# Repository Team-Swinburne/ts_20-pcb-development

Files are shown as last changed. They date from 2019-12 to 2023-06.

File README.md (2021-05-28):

# TS_20 PCB Development

This is the official repository for the PCB development of Team Swinburne FSAE 2020

## Installation & Usage

## Contributing
Pull requests are welcome. For major changes, please open an issue first to discuss what you would like to change.

Please make sure to update tests as appropriate.

## License
[MIT](https://choosealicense.com/licenses/mit/)

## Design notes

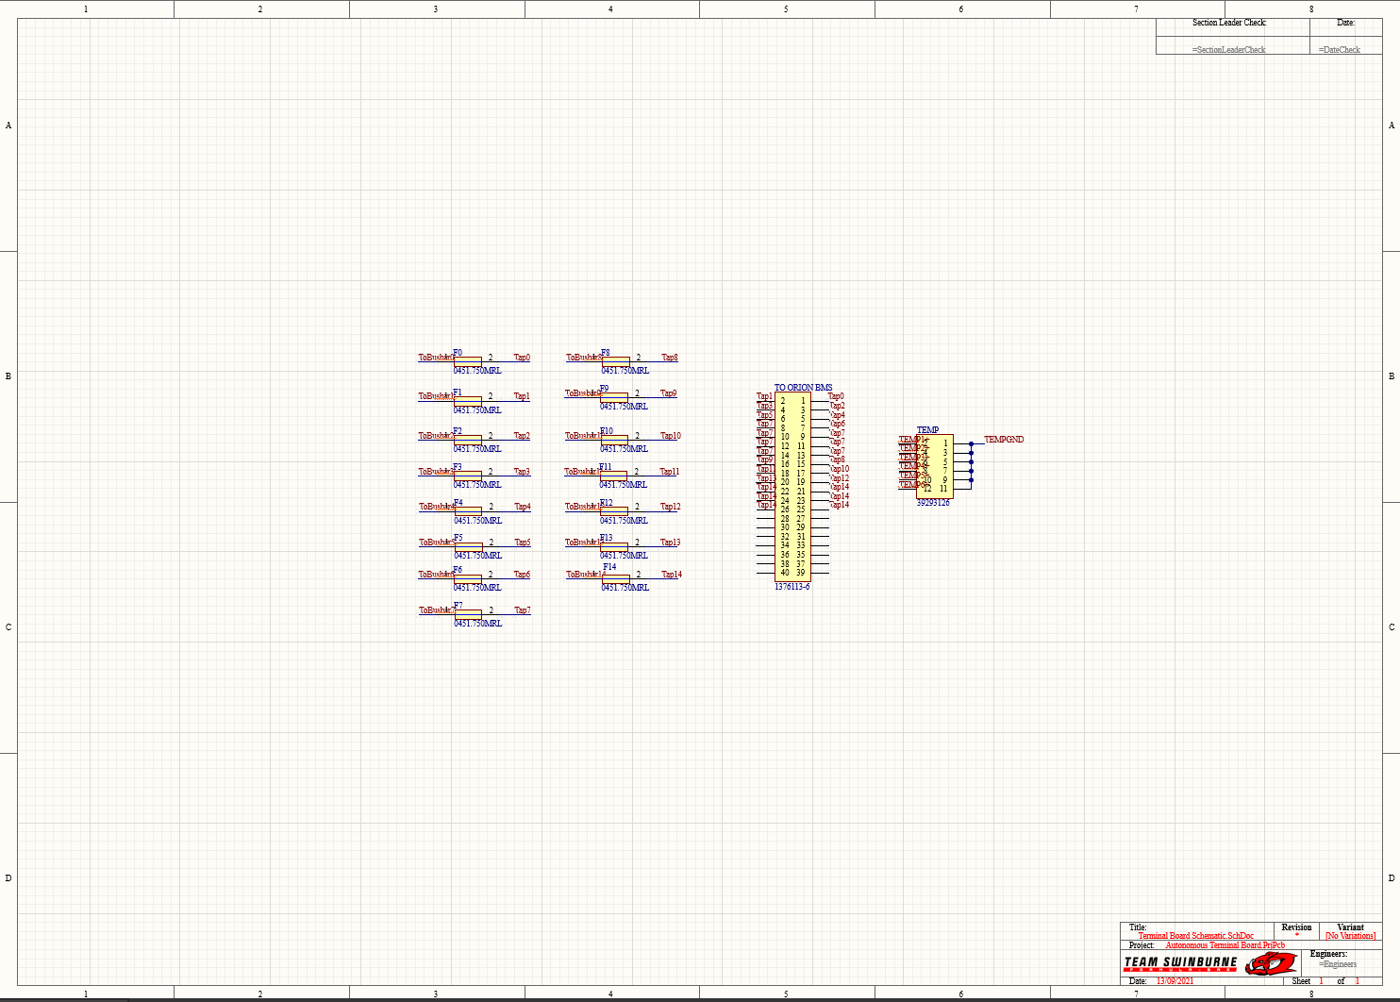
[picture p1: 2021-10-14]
ts_20_Autonomous-Terminal-Board/Autonomous Terminal Board/Photos/Schematic 13 Sep.PNG

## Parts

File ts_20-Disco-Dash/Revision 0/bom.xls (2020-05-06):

Comment | Description | Designator | Footprint | LibRef | Quantity | Colour | Digikey Part Number | Value
LED | Red LED Indication - Discrete 1.75V 0805 (2012 Metric) | 5V ACTIVE, 5V ACTIVE (ISO) | 0805 LED | SML-210LTT86 | 2 | Red | 511-1286-1-ND
RED | LED RED CLEAR 5MM ROUND T/H | AMS, BSPD, IMD, PDOC | 5MM LED | C503B-GAN-CB0F0791 | 4 | Green | C503B-GAN-CB0F0791-ND
10nF |  | C8_U_CAN1, C8_U_CAN2, C11_U_CAN1, C11_U_CAN2 | 1206 | GCM3195C2A103JA16D | 4 |  | 490-4978-2-ND | 10nF
100nF |  | C9_U_CAN1, C9_U_CAN2, C10_U_CAN1, C10_U_CAN2, C13_U_CAN1, C13_U_CAN2, C15_U_CAN1, C15_U_CAN2 | 805 | GCM21BR71E104KA37L | 8 |  |  | 100nF
10uF |  | C12_U_CAN1, C12_U_CAN2, C14_U_CAN1, C14_U_CAN2, C20 | 805 | GRM21BR6YA106KE43L | 5 |  | 490-10514-6-ND | 10uF
100pF |  | C16_U_CAN1, C16_U_CAN2, C17_U_CAN1, C17_U_CAN2, C18_U_CAN1, C18_U_CAN2, C19_U_CAN1, C19_U_CAN2 | 805 | GCM21B5C1H101JA37L | 8 |  |  | 100pF
22uF |  | C21 | 805 | GRM21BR61A226ME51L | 1 |  | 490-10511-1-ND | 22uF
Red | Red LED Indication - Discrete 1.75V 0805 (2012 Metric) | D1, D3, D4, D5, D6, D8, D9, D10, D11, D12, D13, D14 | 0805 LED | SML-210LTT86 | 12 | Red | 511-1286-1-ND
SD560BTR | 1.2V_F 600V 5A SMB | D2 | SMB Diode | SD560BTR | 1 |  | 1655-1530-2-ND
SMAZ5V6-13-F | DIODE ZENER 5.6V 1W SMA | D7 | DI SMA Diode | SMAZ5V6-13-F | 1 |  | SMAZ5V6-FDICT-ND
0ZCF0200AF2C | SMD 24V 2A Fuse | F1 | 2920 | 0ZCF0200AF2C | 1 |  | 507-1749-2-ND
39281063 | Mini-Fit VERT 3x2 | P? | 39281063 | 39281063 | 1 |  | WM3802-ND
BC817-16LT1 | 300mW BJT NPN Transistor | Q1, Q2, Q3, Q4 | ON SOT-23 BJT | BC817-16LT1 | 4 |  | BC817-16LT1OSTR-ND
240R |  | R1, R2, R3, R4 | 805 | RC0805FR07240RL | 4 |  |  | 240R
680R |  | R8, R9, R10, R15 | 805 | RC0805FR07680RL | 4 |  |  | 680R
1k |  | R11, R12, R13, R14 | 805 | RC0805FR071KL | 4 |  |  | 1k
0R |  | R23_U_CAN1, R23_U_CAN2 | 805 | RC0805FR070RL | 2 |  |  | 0R
1.5k |  | R34, R35 | 805 | RC0805FR071K5L | 2 |  |  | 1.5k
DISCO-F469NI | STM32F469 Discovery STM32F4 ARM® Cortex®-M4 MCU 32-Bit Embedded Evaluation Board (The Disco 69 lol) | U1 | DISCO-F469NI | DISCO-F469NI | 1 |  | 497-15990-ND
ADM3053 | Isolated CAN Transceiver | U2_U_CAN1, U2_U_CAN2 | AD SOIC-W 20 | ADM3053 | 2 |  | ADM3053BRWZ-ND
B82787C0104H002 | Common mode choke intended for CANBUS 150mA 50V) | U3_U_CAN1, U3_U_CAN2 | TDK 4-PC Pad | B82787C0104H002 | 2 |  | 495-4598-2-ND
NUP2105L | Dual Line CAN Bus Protector | U4_U_CAN1, U4_U_CAN2 | ON SOT-23 | NUP2105L | 2 |  | NUP2105LT1GOSCT-ND
R-78C5.0-1.0 | CONV DC/DC 1A 5V OUT SIP VERT | U9 | RECOM 3-SIP | R-78C5.0-1.0 | 1 |  | 945-1395-5-ND
RI-0505S | 5V DC-DC Converter (2W) | U10 | RECOM 4-SIP | RI-0505S | 1 |  | 945-1189-ND
744272121 | Common Mode Choke 120UH 2.5A 2LN 460 OHM SMD | U11 | Wurth 4-PC Pad | 744272121 | 1 |  | 732-1489-2-ND
DT13-12P |  | UNIVERSAL1 | DT13-12P | DT13-12P[[/\]]DT13-12P | 1 |  | 1734-1451-ND

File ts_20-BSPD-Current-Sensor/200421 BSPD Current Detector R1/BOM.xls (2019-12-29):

Comment | Description | Designator | Footprint | LibRef | Quantity | Colour
0mm |  | 0V, 5kW OUT, 5V, GLV+, POST AMP, PREAMP, REF | TH Test Point | TH Test Point | 7
10uF |  | C1 | 805 | GRM21BR6YA106KE43L | 1
22uF |  | C2 | 1206 | CC1206MKX5R7BB226 | 1
100nF |  | C3, C4, C5, C6 | 805 | GCM21BR71E104KA37L | 4
SD560BTR | 1.2V_F 600V 5A SMB | D1 | SMB Diode | SD560BTR | 1
Blue | LED BLUE CLEAR 2012 SMD | D2 | 0805 LED | SML-MN2BCTT86C | 1 | Blue
0ZCF0200AF2C | SMD 24V 2A Fuse | F1 | 2920 | 0ZCF0200AF2C | 1
26013115 |  | P1 | 26013115 | 26013115 | 1
DT13-12P |  | P4 | DT13-12P | DT13-12P[[/\]]DT13-12P | 1
30k |  | PULL DOWN! | 805 | RC0805FR0730KL | 1
2N7002K | 60V 380mA, NFET MOSTFET (Small Signal) | Q1 | ON SOT-23 MOSFET | 2N7002K | 1
10k |  | R1 | 805 | RC0805FR0710KL | 1
1k |  | R2, R5 | 805 | RC0805FR071KL | 2
10K (Var) |  | R3 | B 3296 | 3296W-1-103LF | 1
100R |  | R4 | 805 | RC0805FR07100RL | 1
1.5k |  | R6 | 805 | RC0805FR071K5L | 1
3k |  | R7 | 805 | RC0805FR073KL | 1
R-78C5.0-1.0 | CONV DC/DC 1A 5V OUT SIP VERT | U1 | RECOM 3-SIP | R-78C5.0-1.0 | 1
744272121 | Common Mode Choke 120UH 2.5A 2LN 460 OHM SMD | U2 | Wurth 4-PC Pad | 744272121 | 1
LMV339IDR | Comparator General Purpose Open Collector 14-SOIC | U3 | TI 14-SOIC | LMV339IDR | 1
LM324D | IC OPAMP GP 4 CIRCUIT 14SOIC | U4 | TI 14-SOIC | LM324D | 1

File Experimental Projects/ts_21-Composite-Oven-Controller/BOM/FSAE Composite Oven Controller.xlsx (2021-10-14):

Comment | Description | Designator | Footprint | Quantity | Supplier 1 | Supplier Part Number 1
0mm |  | 3.3V, 5V, GND, OD1, OI1, OS, Oven inc 1, Oven set | SMD Test Point | 11
Boot jumper |  | BOOT | TH 2.54mm Header 2x3 | 1
10uF |  | C1 | 0805 | 1
100nF |  | C2, C4, C10, C11, C12, C13 | 0805 | 6
1uF |  | C3, C5, C9 | 0805 | 3
22nF |  | C6 | 0805 | 1
22pF |  | C7, C8 | 0805 | 2
SD560BTR | 1.2V_F 600V 5A SMB | D1 | SMB Diode | 1 |  | 1655-1530-2-ND
Red | Red LED Indication - Discrete 1.75V 0805 (2012 Metric) | D2, D3 | 0805 LED | 2 |  | 511-1286-1-ND, [NoParam]
ST7735 header | Header for the ST7735 LCD module | LCD | TH 2.54mm Header 1x8 | 1 | Digi-Key | 1528-1536-ND
DT13-4P |  | P1 | DT13-4P | 1
10M |  | R1 | 0805 | 1
1k |  | R2, R3, R6, R8, R11 | 0805 | 5
5.1k |  | R4, R5, R9, R10 | 0805 | 4
10k |  | R7, R12, R13, R14, R15 | 0805 | 5
Rotary Encoder |  | S1 | Rotary Encoder | 1 | Digi-Key | PEC11R-4220K-S0024-ND
STLINK 2.54mm | Header used for the STLINK programmer | STLINK | TH 2.54mm Header 1x4 | 1
STM32F103C8T6 | ARM® Cortex®-M3 STM32F1 Microcontroller IC 32-Bit 72MHz 64KB (64K x 8) FLASH | U1 | STM 48-LQFP | 1 | Digi-Key | 497-6063-ND
RT9193-33GB |  | U2 | SOT23-5 IPC | 1 | Digi-Key | 1028-1014-1-ND
TLP291(Y-TP,SE |  | U3, U4, U5 | SOIC-4 (4.55mm width) | 3 | Digi-Key | TLP291(Y-TPSECT-ND
24FC01T-E/OT | I2C EEPROM | U6 | SOT23-5 IPC | 1 | Digi-Key | 24FC01T-E/OTCT-ND
UART 2.54mm |  | UART | TH 2.54mm Header 1x3 | 1
USB4085-GF-A |  | USB | USB4085-GF-A | 1
8MHz |  | X1 | Abracon HC-49/US | 1 | Digi-Key | 535-10212-2-ND

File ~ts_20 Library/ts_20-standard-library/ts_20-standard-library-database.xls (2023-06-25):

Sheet: Fuses
Manufacturer | Part Number | Description | Library Ref | Library Path | Footprint Ref | Footprint Path | Digikey Part Number | Digikey Link
LittelFuse Inc | RKEF300 | 60V 3A Reset Fuse | PTC Fuse | analogue.SchLib | 5mm Leaded | through.PcbLib | RKEF300HF-ND | https://www.digikey.com/product-detail/en/littelfuse-inc/RKEF300/RKEF300HF-ND/5130274
Bel Fuse Inc | 0ZCF0200AF2C | SMD 24V 2A Fuse | PTC Fuse | analogue.SchLib | 2920 | surface.PcbLib | 507-1749-2-ND | https://www.digikey.com/product-detail/en/bel-fuse-inc/0ZCF0200AF2C/507-1749-2-ND/4156090
LittelFuse Inc | 0154.750DR | FUSE BOARD MNT 750MA 125VAC/VDC | Fuse | analogue.SchLib | Omni BLOK 0154 | surface.PcbLib | F1221CT-ND | https://www.digikey.com/product-detail/en/littelfuse-inc/0154.750DR/F1221CT-ND/183370
Littelfuse Inc. | 01530008Z | FUSE HOLDER BLADE 32V 15A PCB | PTC Fuse | analogue.SchLib | LF Holder | through.PcbLib | F065-ND | https://www.digikey.com.au/product-detail/en/littelfuse-inc/01530008Z/F065-ND/183334
Littelfuse Inc. | 0ZCF0100AF2A | PTC RESET FUSE 60V 1A 292 | PTC Fuse | analogue.SchLib | 2920 | surface.PcbLib | 507-2070-1-ND | https://www.digikey.com/product-detail/en/bel-fuse-inc/0ZCF0100AF2A/507-2070-1-ND/6210547

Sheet: Inductors
Manufacturer | Part Number | Description | Value | Impedence | Tolerance | Material | Rated Current | Library Ref | Library Path | Footprint Ref | Footprint Path | Digikey Part Number | Digikey Link
TDK Corportation | MMZ2012Y202BTD25 |  | Ferrite | 2 kOhms @ 100MHz |  | Ferrite Bead | 400mA | Inductor | analogue.SchLib | 0805 | surface.PcbLib | 445-172872-1-ND
Recom | RLS-126 |  | 12uH | 230mOhm | 20% | Wirewound | 800mA | Inductor | analogue.SchLib | 1812 | surface.PcbLib | 945-3429-ND
EPCOS (TDK) | B82787C0104H002 | 100µH @ 100kHz 2 Line Common Mode Choke Surface Mount 5.8 kOhms @ 10MHz 150mA DCR 2Ohm | 100µH @ 100kHz | 5.8 kOhms @ 10MHz |  | Wirewound | 150mA | B82787C0104H002 | integrated.SchLib | TDK 4-PC Pad | surface.PcbLib | 495-4598-1-ND | https://www.digikey.com/product-detail/en/epcos-tdk/B82787C0104H002/495-4598-2-ND/3680998
Wurth Electronics Inc | 744272121 | 120µH @ 100kHz 2 Line Common Mode Choke Surface Mount 460 Ohms @ 30MHz 2.5A DCR 25mOhm | 120uH @ 100kHz | 460 Ohms @ 30MHz |  | Wirewound | 2.5A | 744272121 | integrated.SchLib | Wurth 4-PC Pad | surface.PcbLib | 732-1489-1-ND | https://www.digikey.com/product-detail/en/w-rth-elektronik/744272121/732-1489-1-ND/1639501
Wurth Electronics Inc | 744273501 | 5µH @ 100kHz 2 Line Common Mode Choke Surface Mount 500 Ohms @ 130MHz 5A DCR 5.5mOhm | 5µH @ 100kHz | 500 Ohms @ 130MHz |  | Wirewound | 5A | 744273501 | integrated.SchLib | Wurth 4-PC Pad | surface.PcbLib | 732-2214-6-ND | https://www.digikey.com/product-detail/en/w-rth-elektronik/744273501/732-2214-6-ND/2175826

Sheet: Resistors
Manufacturer | Part Number | Value | Tolerance | Material | Rated Voltage | Library Ref | Library Path | Footprint Ref | Footprint Path | Digikey Part Number
YAGEO | RC0805FR070RL | 0R | 1% | FR-07 | 0.125W | Resistor | analogue.SchLib | 0805 | surface.PcbLib | 311-0.0CRCT-ND
YAGEO | RC0805FR071RL | 1R | 1% | FR-07 | 0.125W | Resistor | analogue.SchLib | 0805 | surface.PcbLib | 311-1.00CRCT-ND
YAGEO | RC0805FR071R2L | 1.2R | 1% | FR-07 | 0.125W | Resistor | analogue.SchLib | 0805 | surface.PcbLib | 311-1.20CRCT-ND
YAGEO | RC0805FR071R3L | 1.3R | 1% | FR-07 | 0.125W | Resistor | analogue.SchLib | 0805 | surface.PcbLib | 311-1.30CRCT-ND
YAGEO | RC0805FR071R5L | 1.5R | 1% | FR-07 | 0.125W | Resistor | analogue.SchLib | 0805 | surface.PcbLib | 311-1.50CRCT-ND
YAGEO | RC0805FR071R6L | 1.6R | 1% | FR-07 | 0.125W | Resistor | analogue.SchLib | 0805 | surface.PcbLib | 311-1.60CRCT-ND
YAGEO | RC0805FR071R8L | 1.8R | 1% | FR-07 | 0.125W | Resistor | analogue.SchLib | 0805 | surface.PcbLib | 311-1.80CRCT-ND
YAGEO | RC0805FR072RL | 2R | 1% | FR-07 | 0.125W | Resistor | analogue.SchLib | 0805 | surface.PcbLib | 311-2.00CRCT-ND
YAGEO | RC0805FR072R2L | 2.2R | 1% | FR-07 | 0.125W | Resistor | analogue.SchLib | 0805 | surface.PcbLib | 311-2.20CRCT-ND
YAGEO | RC0805FR072R4L | 2.4R | 1% | FR-07 | 0.125W | Resistor | analogue.SchLib | 0805 | surface.PcbLib | 311-2.40CRCT-ND
YAGEO | RC0805FR072R7L | 2.7R | 1% | FR-07 | 0.125W | Resistor | analogue.SchLib | 0805 | surface.PcbLib | 311-2.70CRCT-ND
YAGEO | RC0805FR073RL | 3R | 1% | FR-07 | 0.125W | Resistor | analogue.SchLib | 0805 | surface.PcbLib | 311-3.00CRCT-ND
YAGEO | RC0805FR073R3L | 3.3R | 1% | FR-07 | 0.125W | Resistor | analogue.SchLib | 0805 | surface.PcbLib | 311-3.30CRCT-ND
YAGEO | RC0805FR073R6L | 3.6R | 1% | FR-07 | 0.125W | Resistor | analogue.SchLib | 0805 | surface.PcbLib | 311-3.60CRCT-ND
YAGEO | RC0805FR073R9L | 3.9R | 1% | FR-07 | 0.125W | Resistor | analogue.SchLib | 0805 | surface.PcbLib | 311-3.90CRCT-ND
YAGEO | RC0805FR074R3L | 4.3R | 1% | FR-07 | 0.125W | Resistor | analogue.SchLib | 0805 | surface.PcbLib | 311-4.30CRCT-ND
YAGEO | RC0805FR074R7L | 4.7R | 1% | FR-07 | 0.125W | Resistor | analogue.SchLib | 0805 | surface.PcbLib | 311-4.70CRCT-ND
YAGEO | RC0805FR075R1L | 5.1R | 1% | FR-07 | 0.125W | Resistor | analogue.SchLib | 0805 | surface.PcbLib | 311-5.10CRCT-ND
YAGEO | RC0805FR075R6L | 5.6R | 1% | FR-07 | 0.125W | Resistor | analogue.SchLib | 0805 | surface.PcbLib | 311-5.60CRCT-ND
YAGEO | RC0805FR076R2L | 6.2R | 1% | FR-07 | 0.125W | Resistor | analogue.SchLib | 0805 | surface.PcbLib | 311-6.20CRCT-ND
YAGEO | RC0805FR076R8L | 6.8R | 1% | FR-07 | 0.125W | Resistor | analogue.SchLib | 0805 | surface.PcbLib | 311-6.80CRCT-ND
YAGEO | RC0805FR077R5L | 7.5R | 1% | FR-07 | 0.125W | Resistor | analogue.SchLib | 0805 | surface.PcbLib | 311-7.50CRCT-ND
YAGEO | RC0805FR078R2L | 8.2R | 1% | FR-07 | 0.125W | Resistor | analogue.SchLib | 0805 | surface.PcbLib | 311-8.20CRCT-ND
YAGEO | RC0805FR079R1 | 9.1R | 1% | FR-07 | 0.125W | Resistor | analogue.SchLib | 0805 | surface.PcbLib | 311-9.10CRCT-ND
YAGEO | RC0805FR0710RL | 10R | 1% | FR-07 | 0.125W | Resistor | analogue.SchLib | 0805 | surface.PcbLib | 311-10.0CRCT-ND
YAGEO | RC0805FR0711RL | 11R | 1% | FR-07 | 0.125W | Resistor | analogue.SchLib | 0805 | surface.PcbLib | 311-11.0CRCT-ND
YAGEO | RC0805FR0712RL | 12R | 1% | FR-07 | 0.125W | Resistor | analogue.SchLib | 0805 | surface.PcbLib | 311-12.0CRCT-ND
YAGEO | RC0805FR0713RL | 13R | 1% | FR-07 | 0.125W | Resistor | analogue.SchLib | 0805 | surface.PcbLib | 311-13.0CRCT-ND
YAGEO | RC0805FR0715RL | 15R | 1% | FR-07 | 0.125W | Resistor | analogue.SchLib | 0805 | surface.PcbLib | 311-15.0CRCT-ND
YAGEO | RC0805FR0716RL | 16R | 1% | FR-07 | 0.125W | Resistor | analogue.SchLib | 0805 | surface.PcbLib | 311-16.0CRCT-ND
YAGEO | RC0805FR0718RL | 18R | 1% | FR-07 | 0.125W | Resistor | analogue.SchLib | 0805 | surface.PcbLib | 311-18.0CRCT-ND
YAGEO | RC0805FR0720RL | 20R | 1% | FR-07 | 0.125W | Resistor | analogue.SchLib | 0805 | surface.PcbLib | 311-20.0CRCT-ND
YAGEO | RC0805FR0722RL | 22R | 1% | FR-07 | 0.125W | Resistor | analogue.SchLib | 0805 | surface.PcbLib | 311-22.0CRCT-ND
YAGEO | RC0805FR0724RL | 24R | 1% | FR-07 | 0.125W | Resistor | analogue.SchLib | 0805 | surface.PcbLib | 311-24.0CRCT-ND
YAGEO | RC0805FR0727RL | 27R | 1% | FR-07 | 0.125W | Resistor | analogue.SchLib | 0805 | surface.PcbLib | 311-27.0CRCT-ND

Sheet: Diodes
Manufacturer | Description | Vf | Vbr | Part Number | Library Ref | Library Path | Footprint Ref | Footprint Path | Digikey Part Number | Digikey Link | Alternative Parts
SMC Diode Solutions | 1.2V_F 600V 5A SMB |  |  | SD560BTR | Diode | analogue.SchLib | SMB Diode | surface.PcbLib | 1655-1530-2-ND | https://www.digikey.com/product-detail/en/smc-diode-solutions/SD560BTR/1655-1530-2-ND/6022620
Diodes Inc | 18V Zener 1W SND |  |  | SMAZ18-13-F | Zener Diode | analogue.SchLib | SMA Diode | surface.PcbLib | SMAZ18-FDITR-ND | https://www.digikey.com/product-detail/en/diodes-incorporated/SMAZ18-13-F/SMAZ18-FDITR-ND/814767
On Semiconductor | Zener Diode 5.1V 500mW ±5% Surface Mount SOD-123 |  |  | MMSZ5231B-TP | Zener Diode | analogue.SchLib | SOD-123 Diode | surface.PcbLib | MMSZ5231B-TPMSCT-ND | https://www.digikey.com/product-detail/en/micro-commercial-co/MMSZ5231B-TP/MMSZ5231B-TPMSCT-ND/1793361
Diodes Inc | DIODE ZENER 12.43V 500MW SOD323F |  |  | DDZ13ASF-7 | Zener Diode | analogue.SchLib | DI SOD-323F Diode | surface.PcbLib | DDZ13ASF-7DICT-ND | https://www.digikey.com/product-detail/en/diodes-incorporated/DDZ13ASF-7/DDZ13ASF-7DICT-ND/3451540
Diodes Inc | DIODE ZENER 5.6V 1W SMA |  |  | SMAZ5V6-13-F | Zener Diode | analogue.SchLib | DI SMA Diode | surface.PcbLib | SMAZ5V6-FDICT-ND | https://www.digikey.com/product-detail/en/diodes-incorporated/SMAZ5V6-13-F/SMAZ5V6-FDICT-ND/755500
Diodes Inc | DIODE ZENER 51V 3W SMB |  |  | 1SMB5942B-13 | Zener Diode | analogue.SchLib | DI SMB Diode | surface.PcbLib | 1SMB5942B-13DICT-ND | https://www.digikey.com/product-detail/en/diodes-incorporated/1SMB5942B-13/1SMB5942B-13DICT-ND/5054245
On Semiconductor | DIODE GEN PURP 100V 200MA SOD80 |  |  | FDLL4148-D87Z | Diode | analogue.SchLib | SOD-80 Diode | surface.PcbLib | FDLL4148-D87ZCT-ND | https://www.digikey.com/product-detail/en/on-semiconductor/FDLL4148-D87Z/FDLL4148-D87ZCT-ND/3042567
ST | 42.8V Clamp 93A (8/20µs) Ipp Tvs Diode Surface Mount SMB (DO-214AA) | 42.8 | 42.8V | SM6T39CAY | Bidirectional Zener Diode | analogue.SchLib | ST SMB Diode | surface.PcbLib | SM6T39CAY | https://www.digikey.com/en/products/detail/stmicroelectronics/SM6T39CAY/2442903 | https://www.digikey.com/en/products/detail/stmicroelectronics/SM6T39AY/2442901

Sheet: LEDs
Manufacturer | Part Number | Description | Colour | Library Ref | Library Path | Footprint Ref | Footprint Path | Digikey Part Number | Digikey Link
Cree Inc. | C503B-GAN-CB0F0791 | LED GREEN CLEAR 5MM ROUND T/H | Green | LED | analogue.SchLib | 5MM LED | through.PcbLib | C503B-GAN-CB0F0791-ND | https://www.digikey.com/products/en?mpart=C503B-GAN-CB0F0791&v=90
Broadcom Limited | HSMM-C150 | LED GREEN DIFFUSED CHIP SMD | Green | LED | analogue.SchLib | 1206 LED GREEN | surface.PcbLib | HSMM-C150-ND | https://www.digikey.com/product-detail/en/broadcom-limited/HSMM-C150/HSMM-C150-ND/1234707
Broadcom Limited | HSMC-C150 | LED RED DIFFUSED CHIP SMD | Red | LED | analogue.SchLib | 1206 LED RED | surface.PcbLib | 516-2825-6-ND | https://www.digikey.com/product-detail/en/broadcom-limited/HSMC-C150/516-2825-6-ND/3909256
ROHM Semiconductor | SML-210FTT86 | Green LED Indication - Discrete 1.75V 0805 (2012 Metric) | Green | LED | analogue.SchLib | 0805 LED | surface.PcbLib | 511-1285-1-ND | https://www.digikey.com/product-detail/en/rohm-semiconductor/SML-210FTT86/511-1285-1-ND/637098
ROHM Semiconductor | SML-211DTT86 | Orange LED Indication - Discrete 1.75V 0805 (2012 Metric) | Orange | LED | analogue.SchLib | 0805 LED | surface.PcbLib | 511-1291-1-ND | https://www.digikey.com/product-detail/en/rohm-semiconductor/SML-211DTT86/511-1291-1-ND/637104
ROHM Semiconductor | SML-211YTT86 | Yellow LED Indication - Discrete 1.75V 0805 (2012 Metric) | Yellow | LED | analogue.SchLib | 0805 LED | surface.PcbLib | 511-1293-1-ND | https://www.digikey.com/product-detail/en/rohm-semiconductor/SML-211YTT86/511-1293-1-ND/637106
ROHM Semiconductor | SML-210LTT86 | Red LED Indication - Discrete 1.75V 0805 (2012 Metric) | Red | LED | analogue.SchLib | 0805 LED | surface.PcbLib | 511-1286-1-ND | https://www.digikey.com/product-detail/en/rohm-semiconductor/SML-210LTT86/511-1286-1-ND/637099
ROHM Semiconductor | SML-MN2BCTT86C | LED BLUE CLEAR 2012 SMD | Blue | LED | analogue.SchLib | 0805 LED | surface.PcbLib | 846-1207-1-ND | https://www.digikey.com/product-detail/en/rohm-semiconductor/SMLMN2BCTT86C/846-1207-1-ND/6057239
 |  |  | RGB | LED | analogue.SchLib | HOTRED RGB_LED | surface.PcbLib |  | https://www.aliexpress.com/item/32943617217.html?spm=a2g0s.9042311.0.0.99a74c4d1Dy1p4

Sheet: Transistors
Manufacturer | Part Number | Description | Library Ref | Library Path | Footprint Ref | Footprint Path | Digikey Part Number | Digikey Link | Qty
ON Semiconductor | 2N7002K | 60V 380mA, NFET MOSTFET (Small Signal) | MOSFET-N | analogue.SchLib | ON SOT-23 MOSFET | surface.PcbLib | 2N7002KCT-ND | https://www.digikey.com/product-detail/en/on-semiconductor/2N7002K/2N7002KCT-ND/2060375 | 30
ON Semiconductor | BC817-16LT1 | 300mW BJT NPN Transistor | NPN | analogue.SchLib | ON SOT-23 BJT | surface.PcbLib | BC817-16LT1OSTR-ND | https://www.digikey.com.au/product-detail/en/on-semiconductor/BC817-16LT1/BC817-16LT1OSTR-ND/606178
STMicroelectronics | STD70N10F4 | N-Channel 100V 60A (Tc) 125W (Tc) Surface Mount DPAK | MOSFET-N | analogue.SchLib | STM TO-252 MOSFET | surface.PcbLib | 497-8806-2-ND | https://www.digikey.com/product-detail/en/stmicroelectronics/STD70N10F4/497-8806-2-ND/2035599
ON Semiconductor | 2N7000 | MOSFET N-CH 60V 200MA TO-92 | MOSFET-N | analogue.SchLib | ON TO-92 | through.PcbLib | 2N7000FS-ND | https://www.digikey.com.au/product-detail/en/on-semiconductor/2N7000/2N7000FS-ND/244278
STMicroelectronics | STB14NM50N | MOSFET N-CH 500V 12A D2PAK | MOSFET-N | analogue.SchLib | STM TO-263-3 MOSFET | surface.PcbLib | 497-10644-1-ND | https://www.digikey.hu/product-detail/en/stmicroelectronics/STB14NM50N/497-10644-1-ND/2346721
ON Semiconductor | BC858ALT1G | TRANS PNP 30V 0.1A SOT-23 | PNP | analogue.SchLib | ON TO-236-3 BJT | surface.PcbLib | BC858ALT1GOSCT-ND | https://www.digikey.com.au/product-detail/en/on-semiconductor/BC858ALT1G/BC858ALT1GOSCT-ND/3462248
ON Semiconductor | BC848ALT1G | TRANS NPN 30V 0.1A SOT23 | NPN | analogue.SchLib | ON TO-236-3 BJT | surface.PcbLib | BC848ALT1GOSCT-ND | https://www.digikey.com/product-detail/en/on-semiconductor/BC848ALT1G/BC848ALT1GOSCT-ND/917837
ON Semiconductor | MMBT489LT1G | TRANS NPN 30V 1A SOT23 | NPN | analogue.SchLib | ON SOT-23 BJT | surface.PcbLib | MMBT489LT1GOSCT-ND | https://www.digikey.com.au/product-detail/en/on-semiconductor/MMBT489LT1G/MMBT489LT1GOSCT-ND/2623471
Infineon Technologies | BSS308PEH6327XTSA1 | P-Channel 30V 2A (Ta) 500mW (Ta) Surface Mount SOT-23-3 | MOSFET-P | analogue.SchLib | IN SOT-23 MOSFET | surface.PcbLib | BSS308PEH6327XTSA1CT-ND | https://www.digikey.com/product-detail/en/infineon-technologies/BSS308PEH6327XTSA1/BSS308PEH6327XTSA1CT-ND/3196649
ON Semiconductor | NSV1C201MZ4T1G | Bipolar (BJT) Transistor NPN 100V 2A 100MHz 800mW Surface Mount SOT-223 (TO-261) | NPN | analogue.SchLib | ON SOT-223 BJT | surface.PcbLib | NSV1C201MZ4T1GOSCT-ND | https://www.digikey.com/product-detail/en/on-semiconductor/NSV1C201MZ4T1G/NSV1C201MZ4T1GOSCT-ND/5969293
Rohm Semiconductor | R6015ENJTL | MOSFET N-CH 600V 15A LPT | MOSFET-N | analogue.SchLib | R TO-263 N-MOSFET | surface.PcbLib | R6015ENJTLCT-ND | https://www.digikey.com.au/product-detail/en/rohm-semiconductor/R6015ENJTL/R6015ENJTLCT-ND/5042516
ON Semiconductor | 2SK3666 | JFET N-Channel 10mA 200mW Surface Mount 3-CP | JFET-N | analogue.SchLib | ON SOT-23 JFET | surface.PcbLib | 869-1107-1-ND | https://www.digikey.com/product-detail/en/on-semiconductor/2SK3666-3-TB-E/869-1107-1-ND/2165585

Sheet: Crystals
Manufacturer | Part Number | Value | Load Capacitance | ESR | Library Ref | Library Path | Footprint Ref | Footprint Path | Digikey Part Number | Digikey Link
Abracon LLC | ABLS-8.000MHZ-B4-T | 8MHz | 18pF | 80R | Crystal | analogue.SchLib | Abracon HC-49/US | surface.PcbLib | 535-10212-2-ND | https://www.digikey.com/product-detail/en/abracon-llc/ABLS-8.000MHZ-B4-T/535-10212-2-ND/2184155
EPSON | FC-135 32.7680KA-A5 | 32.768kHz | 12.5pF | 70k | Crystal | analogue.SchLib | EPSON 2-SMD | surface.PcbLib | SER4103TR-ND | https://www.digikey.com/product-detail/en/epson/FC-135-32.7680KA-A5/SER4103TR-ND/5259895
Abracon LLC | ABLS-16.000MHZ-B4-T | 16MHz | 18pF | 40R | Crystal | analogue.SchLib | Abracon HC-49/US | surface.PcbLib | 535-10226-1-ND | https://www.digikey.com/product-detail/en/abracon-llc/ABLS-16.000MHZ-B4-T/535-10226-1-ND/2184261
Abracon LLC | ABM8AIG-16.000MHZ-12-2Z-T3 | 16MHz | 12pF | 70R | Crystal (Shielded) | analogue.SchLib | Abracon 4-SMD 3.2x2.5 | surface.PcbLib | 535-13386-1-ND | https://www.digikey.com/en/products/detail/abracon-llc/ABM8AIG-16-000MHZ-12-2Z-T3/5817586

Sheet: Regulators
Manufacturer | Part Number | Description | Input Voltage | Output Voltage | Output Power | Efficiency | Isolation | Library Ref | Library Path | Footprint Ref | Footprint Path | Digikey Part Number | Digikey Link
Recom | RI-0505S/P | 5V DC-DC Converter (2W) (Short circuit protected) | 4.5V | 5.5V | 2W | 83% | Isolated | RI-0505S | integrated.SchLib | RECOM 4-SIP | through.PcbLib | 945-1499-5-ND | https://www.digikey.com/product-detail/en/recom-power/RI-0505S-P/945-1499-5-ND/2314368
Recom | R-78C12-1.0 | 3PIN DC DC CONVERTER 12V 12W |  | 12V | 12W |  | Non-Isolated | R-78C12-1.0 | integrated.SchLib | RECOM 3-SIP | through.PcbLib | 945-1392-5-ND | https://www.digikey.com/products/en/power-supplies-board-mount/dc-dc-converters/922?k=R-78C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
Recom | RI-1205S | Isolated Module DC DC Converter 1 Output 5V 400mA 10.8V - 13.2V Input | 10.8V-13.2V | 5V | 2W |  | Isolated | RI-1205S | integrated.SchLib | RECOM 4-SIP | through.PcbLib | 945-1191-ND | https://www.digikey.com/product-detail/en/recom-power/RI-1205S/945-1191-ND/2256371
Recom | RI-0512S | Isolated Module DC DC Converter 1 Output 12V 167mA 4.5V - 5.5V Input | 4.5V-5.5V | 12V | 1W |  | Isolated | RI-0512S | integrated.SchLib | RECOM 4-SIP | through.PcbLib | 945-1190-ND | https://www.digikey.com/product-detail/en/recom-power/RI-0512S/945-1190-ND/2256370
Recom | RI-1212S/P | 4PIN DC DC CONVERTER 12V 2W |  | 12V | 2W |  | Isolated | RI-1212S/P | integrated.SchLib | RECOM 4-SIP | through.PcbLib | 945-3358-ND | https://www.digikey.com/product-detail/en/recom-power/RI-1212S-P/945-3358-ND/2314373
Recom | R-78C3.3-1.0 | CONV DC/DC 1A 3.3V OUT SIP VERT |  | 3.3V |  |  | Non-Isolated | R-78C3.3-1.0 | integrated.SchLib | RECOM 3-SIP | through.PcbLib | 945-1394-5-ND | https://www.digikey.com/product-detail/en/recom-power/R-78C3.3-1.0/945-1394-5-ND/2652147
Traco Power | TMR 3-1212WI | DC DC CONVERTER 12V 3W |  | 12V | 3W |  | Isolated | TMR 3-1212WI | integrated.SchLib | TRECO 8-SIP | through.PcbLib | 1951-2367-ND | https://www.digikey.com.au/product-detail/en/traco-power/TMR-3-1212WI/1951-2367-ND/9383402
Recom | R-78C5.0-1.0 | CONV DC/DC 1A 5V OUT SIP VERT |  | 5V | 5W |  | Non-Isolated | R-78C5.0-1.0 | integrated.SchLib | RECOM 3-SIP | through.PcbLib | 945-1395-5-ND | https://www.digikey.com.au/product-detail/en/recom-power/R-78C5.0-1.0/945-1395-5-ND/2652148
XP Power | JTC0424S05 | DC DC CONVERTER 5V 4W | 9V-36V | 5V | 4W | 79% | Isolated | JTC0424S05 | integrated.SchLib | 24-DIP Module, 7 Leads | through.PcbLib | JTC0424S05-ND | https://www.digikey.com/products/en?keywords=%20JTC0424S05
Analog Devices | ADUM6028 | Isolated Module DC DC Converter 1 Output 3.3V, 5V 60mA 4.5V - 5.5V Input | 4.5V-5.5V | 5V, 3.3V | 2W | 33% | Isolated | ADUM6028 | integrated.SchLib | AD 8-SOIC-W | surface.PcbLib | ADUM6028-5BRIZ-ND | https://www.digikey.com/product-detail/en/analog-devices-inc/ADUM6028-5BRIZ/ADUM6028-5BRIZ-ND/9485494
Recom | R2S-053.3/P | Isolated Module DC DC Converter 1 Output 3.3V 606mA 4.5V - 5.5V Input | 4.5V-5.5V | 3.3V | 2W | 75% | Isolated | R2S-053.3/P | integrated.SchLib | RECOM 8-SMD (5 Pin) | surface.PcbLib | 945-2677-5-ND | https://www.digikey.com/product-detail/en/recom-power/R2S-053.3-P/945-2677-5-ND/2302804
Recom | R2S-0505/HP | Isolated Module DC DC Converter 1 Output 3.3V 606mA 4.5V - 5.5V Input | 4.5V-5.5V | 5V | 2W | 85% | Isolated | R2S-0505/HP | integrated.SchLib | RECOM 8-SMD (5 Pin) | surface.PcbLib | 945-1764-5-ND | https://www.digikey.com/product-detail/en/recom-power/R2S-0505-HP/945-1764-5-ND/2302761
Richtek | RT9193-33GB | Linear Voltage Regulator IC 1 Output 300mA SOT-23-5 | 5.5V-0.3V | 3.3V | 1W | 50% | Non-Isolated | RT9193-33GB | integrated.SchLib | RICHTEK SOT-23-5 | surface.PcbLib | 1028-1014-1-ND | https://www.digikey.com/products/en?keywords=1028-1014-1-ND
Texas Instruments | TI LM317DCYR | Linear Voltage Regulator IC 1 Output 1.5A SOT-223-4 | 3V-40V | 1.25V-37V | 1.5A |  | Non-Isolated | TI LM317 | integrated.SchLib | TI SOT-223 | surface.PcbLib | 296-12602-1-ND | https://www.digikey.com/product-detail/en/texas-instruments/LM317DCYR/296-12602-1-ND/443738
Linear Technologies | LT3088EST | Linear Voltage Regulator IC Output 800mA SOT-223-3 | 1.6V-36V | 1.6V-34.5V | 800mA | 50% | Non-Isolated | LT3088EST | integrated.SchLib | LT SOT-223 | surface.PcbLib | LT3088EST#PBF-ND | https://www.digikey.com/en/products/detail/analog-devices-inc/LT3088EST-PBF/5297582

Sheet: Relays
Manufacturer | Part Number | Description | Library Ref | Library Path | Footprint Ref | Footprint Path | Digikey Part Number | Digikey Link
Cynergy 3 | DBT71210 | RELAY REED SPST-NC 2A 12V | DBT71210 | integrated.SchLib | C3 SPST | through.PcbLib | 725-1040-ND | https://www.digikey.com.au/product-detail/en/cynergy-3/DBT71210/725-1040-ND/752037
TE Connectivity | V23105A5303A201 | RELAY TELECOM DPDT 3A 12V | V23105A5303A201 | integrated.SchLib | TI 2-DIL | through.PcbLib | PB387-ND | https://www.digikey.com/product-detail/en/te-connectivity-potter-brumfield-relays/V23105A5303A201/PB387-ND/291023
Axicom | V23105A5475A201 | 5V DPDT Relay 3A 220VDC | V23105A5475A201 | integrated.SchLib | TI 2-DIL | through.PcbLib | PB383-ND | https://www.digikey.com/products/en?mpart=V23105A5001A201&v=41
Cynergy 3 | DAT71210 | RELAY REED SPST-NO 2A 12V | DAT71210 | integrated.SchLib | C3 SPST | through.PcbLib | 725-1030-ND | https://www.digikey.com.au/product-detail/en/cynergy-3/DAT71210/725-1030-ND/752005
Cynergy 3 | DAT70510 | RELAY REED SPST-NO 2A 12V | DAT70510 | integrated.SchLib | C3 SPST | through.PcbLib | 725-1038-ND | https://www.digikey.com.au/product-detail/en/cynergy-3/DBT70510/725-1038-ND/752033
Cynergy 3 | DBT70510 | RELAY REED SPST-NC 2A 5V | DBT70510 | integrated.SchLib | C3 SPST | through.PcbLib | 725-1038-ND | https://www.digikey.com/product-detail/en/cynergy-3/DBT70510/725-1038-ND/752033
TE Connectivity | 9-1462038-9 | RELAY TELECOM DPDT 5A 5V | 9-1462038-9 | integrated.SchLib | TE IM DPDT 2C | surface.PcbLib | PB1172CT-ND | https://www.digikey.com.au/product-detail/en/te-connectivity-potter-brumfield-relays/9-1462038-9/PB1172CT-ND/1828462
Comus International | 3350-1275-056 | RELAY REED HV SPST 200W 3A 5V (NO) | 3350-1275-056 | integrated.SchLib | CI SPST | through.PcbLib | 1835-1036-ND | https://www.digikey.com.au/product-detail/en/comus-international/3350-1275-056/1835-1036-ND/7515918
Comus International | 3350-4275-056 | RELAY REED HV SPST 200W 3A 5V (NC) | 3350-4275-056 | integrated.SchLib | CI SPST | through.PcbLib | 1835-1039-ND | https://www.digikey.com.au/product-detail/en/comus-international/3350-4275-056/1835-1039-ND/7515921
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

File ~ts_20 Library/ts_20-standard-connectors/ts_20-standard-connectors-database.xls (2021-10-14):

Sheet: Deutsch DT
Part Number | Positions | Pitch | Row Spacing | Angle | Flange | Contact | Library Ref | Library Path | Footprint Ref | Footprint Path | Digikey Part Number | Digikey Link
DT13-6P | 6 | 4.44mm | 6.35mm | 90 | Yes | Copper Alloy | DT13-6P | DT.SchLib | DT13-6P | DT.PcbLib | 1734-1025-ND | https://www.digikey.com/product-detail/en/te-connectivity-deutsch-connectors/DT13-6P/1734-1025-ND/6566589
DT13-12P | 12 | 4.44mm | 6.35mm | 90 | Yes | Nickel | DT13-12P | DT.SchLib | DT13-12P | DT.PcbLib | 1734-1451-ND | https://www.digikey.com.au/product-detail/en/te-connectivity-deutsch-connectors/DT13-12PA/1734-1451-ND/7220123
DT13-4P | 4 | 4.44mm | 6.35mm | 90 | Yes | Copper Alloy | DT13-4P | DT.SchLib | DT13-4P | DT.PcbLib | 1734-1024-ND | https://www.digikey.com.au/product-detail/en/te-connectivity-deutsch-connectors/DT13-4P/1734-1024-ND/6566588
DT15-12P | 12 | 4.44mm | 9.12 mm | 0 | Yes | Copper Alloy | DT15-12P | DT.SchLib | DT15-12P | DT.PcbLib | 1734-1027-ND | https://www.digikey.com/product-detail/en/te-connectivity-deutsch-connectors/DT15-12PA/1734-1027-ND/6566591
DTF13-6P | 6 | 4.45mm | 4.45mm | 90 | No | Copper Alloy | DT13-6P | DT.SchLib | DTF13-6P | DT.PcbLib | 1734-1754-ND | https://www.digikey.com/products/en?keywords=DTF13-6P
DTF13-12P | 12 | 4.45mm | 4.45mm | 90 | No | Copper Alloy | DT13-12P | DT.SchLib | DTF13-12P | DT.PcbLib | 1734-1861-ND | https://www.digikey.com/products/en?keywords=dtf13-12pa
DT13-2P | 2 | 4.44mm | 6.35mm | 90 | Yes | Copper Alloy | DT13-2P | DT.SchLib | DT13-2P | DT.PcbLib | 1734-1452-ND | https://www.digikey.com/product-detail/en/te-connectivity-deutsch-connectors/DT13-2P/1734-1452-ND/7220101
DT13-4P | 2 | 4.44mm | 6.35mm | 90 | Yes | Copper Alloy | DT13-4P | DT.SchLib | DT13-4P | DT.PcbLib | 1734-1024-ND | https://www.digikey.com/product-detail/en/te-connectivity-deutsch-connectors/DT13-4P/1734-1024-ND/6566588
DTF13-4P | 4 | 9.12mm | 4.45mm | 90 | Yes | Copper Alloy | DT13-4P | DT.SchLib | DTF13-4P | DT.PcbLib | 1734-1646-ND | https://www.digikey.com.au/products/en?keywords=dtf13-4p
DTF15-12P | 12 | 4.44mm | 9.12 mm | 0 | No | Copper Alloy | DT15-12P | DT.SchLib | DTF15-12P | DT.PcbLib | 1734-1647-ND | https://www.digikey.com.au/product-detail/en/te-connectivity-deutsch-connectors/DTF15-12PA/1734-1647-ND/7220164
 |  |  |  |  |  |  |  |  |  | DT.PcbLib

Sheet: Screw Terminals
Part Number | Positions | Pitch | Row Spacing | Angle | Flange | Contact | Library Ref | Library Path | Footprint Ref | Footprint Path | Digikey Part Number | Digikey Link
1760510000 | 2 | 5.08mm | 0 | 0 | No | NA | Header 1x2 | Screw Terminals.SchLib | TH 5.08mm Header 1x2 | Screw Terminals.PcbLib | 281-1882-ND | https://www.digikey.com.au/product-detail/en/weidm%C3%BCller/1760510000/281-1882-ND/459739
1760520000 | 3 | 5.08mm | 0 | 0 | No | NA | Header 1x3 | Screw Terminals.SchLib | TH 5.08mm Header 1x3 | Screw Terminals.PcbLib | 281-1883-ND | https://www.digikey.com.au/product-detail/en/weidm%C3%BCller/1760520000/281-1883-ND/459740

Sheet: Deutsch DTM
Part Number | Positions | Pitch | Row Spacing | Angle | Flange | Contact | Library Ref | Library Path | Footprint Ref | Footprint Path | Digikey Part Number | Digikey Link
DTM13-12P | 12 | 6.7mm |  | 90 | Yes |  | DTM13-4P | DTM.SchLib | DTM13-4P | DTM.PcbLib
DTM13-12PA-12PB | 24 | 6.7mm |  | 90 |  |  | DTM13-12PA-12PB | DTM.SchLib | DTM13-12PA-12PB | DTM.PcbLib | 1734-1131-ND | https://www.digikey.com.au/product-detail/en/te-connectivity-deutsch-connectors/DTM13-12PA-12PB-R008/1734-1131-ND/6566695
 |  |  |  |  |  |  |  |  |  | DT.PcbLib

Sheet: USB
Part Number | Description | Angle | Library Ref | Library Path | Footprint Ref | Footprint Path | Digikey Part Number | Digikey Link
USB4085-GF-A | USB - C (Type - C) USB 2.0 Receptacle Connector 16 Position Through Hole, Right Angle | 90 | USB4085-GF-A | USB.SchLib | USB4085-GF-A | USB.PcbLib | 2073-USB4085-GF-ACT-ND | https://www.digikey.ee/product-detail/en/gct/USB4085-GF-A/2073-USB4085-GF-ACT-ND/9859733

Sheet: Deutsch DTP
Part Number | Positions | Pitch | Row Spacing | Angle | Flange | Contact | Library Ref | Library Path | Footprint Ref | Footprint Path | Digikey Part Number | Digikey Link
DTP13-4P | 4 | 6.7mm |  | 90 | Yes |  | DTP13-4P | DTP.SchLib | DTP13-4P | DTP.PcbLib

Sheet: Molex Minifit
Part Number | Positions | Pitch | Row Spacing | Angle | Flange | Contact | Library Ref | Library Path | Footprint Ref | Footprint Path | Digikey Part Number | Digikey Link
39300020 | 2 | 4.2mm | 5.5mm | 90 | No | Tin | 2 | Minifit.SchLib | 39300020 | Minifit.PcbLib | WM21351-ND
39300040 | 4 | 4.2mm | 5.5mm | 90 | No | Tin | 4 | Minifit.SchLib | 39300040 | Minifit.PcbLib | WM21352-ND
39300060 | 6 | 4.2mm | 5.5mm | 90 | No | Tin | 6 | Minifit.SchLib | 39300060 | Minifit.PcbLib | WM21353-ND
39300080 | 8 | 4.2mm | 5.5mm | 90 | No | Tin | 8 | Minifit.SchLib | 39300080 | Minifit.PcbLib | WM21354-ND
39300100 | 10 | 4.2mm | 5.5mm | 90 | No | Tin | 10 | Minifit.SchLib | 39300100 | Minifit.PcbLib | WM21355-ND
39300120 | 12 | 4.2mm | 5.5mm | 90 | No | Tin | 12 | Minifit.SchLib | 39300120 | Minifit.PcbLib | WM21356-ND
39300140 | 14 | 4.2mm | 5.5mm | 90 | No | Tin | 14 | Minifit.SchLib | 39300140 | Minifit.PcbLib | WM21357-ND
39300160 | 16 | 4.2mm | 5.5mm | 90 | No | Tin | 16 | Minifit.SchLib | 39300160 | Minifit.PcbLib | WM21358-ND
39300180 | 18 | 4.2mm | 5.5mm | 90 | No | Tin | 18 | Minifit.SchLib | 39300180 | Minifit.PcbLib | WM21359-ND
39300200 | 20 | 4.2mm | 5.5mm | 90 | No | Tin | 20 | Minifit.SchLib | 39300200 | Minifit.PcbLib | WM21360-ND
39300220 | 22 | 4.2mm | 5.5mm | 90 | No | Tin | 22 | Minifit.SchLib | 39300220 | Minifit.PcbLib | WM21361-ND
39300240 | 24 | 4.2mm | 5.5mm | 90 | No | Tin | 24 | Minifit.SchLib | 39300240 | Minifit.PcbLib | WM21362-ND
39293026 | 2 | 4.2mm | 5.5mm | 0 | No | Tin | 2 | Minifit.SchLib | 39293026 | Minifit.PcbLib | WM3843-ND
39293046 | 4 | 4.2mm | 5.5mm | 0 | No | Tin | 4 | Minifit.SchLib | 39293046 | Minifit.PcbLib | WM3844-ND
39293066 | 6 | 4.2mm | 5.5mm | 0 | No | Tin | 6 | Minifit.SchLib | 39293066 | Minifit.PcbLib | WM3845-ND
39293086 | 8 | 4.2mm | 5.5mm | 0 | No | Tin | 8 | Minifit.SchLib | 39293086 | Minifit.PcbLib | WM3846-ND
39293106 | 10 | 4.2mm | 5.5mm | 0 | No | Tin | 10 | Minifit.SchLib | 39293106 | Minifit.PcbLib | WM3847-ND
39293126 | 12 | 4.2mm | 5.5mm | 0 | No | Tin | 12 | Minifit.SchLib | 39293126 | Minifit.PcbLib | WM3848-ND
39293146 | 14 | 4.2mm | 5.5mm | 0 | No | Tin | 14 | Minifit.SchLib | 39293146 | Minifit.PcbLib | WM3849-ND
39293166 | 16 | 4.2mm | 5.5mm | 0 | No | Tin | 16 | Minifit.SchLib | 39293166 | Minifit.PcbLib | WM3850-ND
39293206 | 20 | 4.2mm | 5.5mm | 0 | No | Tin | 20 | Minifit.SchLib | 39293206 | Minifit.PcbLib | WM3851-ND

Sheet: Molex SL
Part Number | Positions | Pitch | Row Spacing | Angle | Flange | Contact | Library Ref | Library Path | Footprint Ref | Footprint Path | Digikey Part Number | Digikey Link
705530015 | 16 | 2.54mm | - | 90 | No | Gold | 705530015 | Molex SL.SchLib | 705530015 | Molex SL.PcbLib | WM4914-ND | https://www.digikey.com/product-detail/en/molex/0705530015/WM4914-ND/531491

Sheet: Molex Micro-Fit
Part Number | Positions | Pitch | Row Spacing | Angle | Flange | Contact | Library Ref | Library Path | Footprint Ref | Footprint Path | Digikey Part Number | Digikey Link
430450228 | 2 | 3.0mm | 3.0mm | 0 | No | Gold | 430450228 | Molex Micro-Fit.SchLib | 430450228 | Molex Micro-Fit.PcbLib | WM10659-ND | https://www.digikey.com/product-detail/en/molex/0430450228/WM10659-ND/3310183
430450428 | 4 | 3.0mm | 3.0mm | 0 | No | Gold | 430450428 | Molex Micro-Fit.SchLib | 430450428 | Molex Micro-Fit.PcbLib | WM10670-ND | https://www.digikey.com/product-detail/en/molex/0430450428/WM10670-ND/3310190
430450628 | 6 | 3.0mm | 3.0mm | 0 | No | Gold | 430450628 | Molex Micro-Fit.SchLib | 430450628 | Molex Micro-Fit.PcbLib | WM10679-ND | https://www.digikey.com/product-detail/en/molex/0430450628/WM10679-ND/3310200
430450828 | 8 | 3.0mm | 3.0mm | 0 | No | Gold | 430450828 | Molex Micro-Fit.SchLib | 430450828 | Molex Micro-Fit.PcbLib | WM10693-ND | https://www.digikey.com/product-detail/en/molex/0430450828/WM10693-ND/3310209
430451028 | 10 | 3.0mm | 3.0mm | 0 | No | Gold | 430451028 | Molex Micro-Fit.SchLib | 430451028 | Molex Micro-Fit.PcbLib | WM10696-ND | https://www.digikey.com/product-detail/en/molex/0430451028/WM10696-ND/3310216
430451228 | 12 | 3.0mm | 3.0mm | 0 | No | Gold | 430451228 | Molex Micro-Fit.SchLib | 430451228 | Molex Micro-Fit.PcbLib | WM10705-ND | https://www.digikey.com/product-detail/en/molex/0430451228/WM10705-ND/3310226
430451428 | 14 | 3.0mm | 3.0mm | 0 | No | Gold | 430451428 | Molex Micro-Fit.SchLib | 430451428 | Molex Micro-Fit.PcbLib | WM10720-ND | https://www.digikey.com/product-detail/en/molex/0430451428/WM10720-ND/3310241
430451628 | 16 | 3.0mm | 3.0mm | 0 | No | Gold | 430451628 | Molex Micro-Fit.SchLib | 430451628 | Molex Micro-Fit.PcbLib | WM10719-ND | https://www.digikey.com/product-detail/en/molex/0430451628/WM10719-ND/3310256
430451828 | 18 | 3.0mm | 3.0mm | 0 | No | Gold | 430451828 | Molex Micro-Fit.SchLib | 430451828 | Molex Micro-Fit.PcbLib | WM10736-ND | https://www.digikey.com/product-detail/en/molex/0430451828/WM10736-ND/3310275
430452028 | 20 | 3.0mm | 3.0mm | 0 | No | Gold | 430452028 | Molex Micro-Fit.SchLib | 430452028 | Molex Micro-Fit.PcbLib | WM10733-ND | https://www.digikey.com/product-detail/en/molex/0430452028/WM10733-ND/3310292
430452228 | 22 | 3.0mm | 3.0mm | 0 | No | Gold | 430452228 | Molex Micro-Fit.SchLib | 430452228 | Molex Micro-Fit.PcbLib | WM10740-ND | https://www.digikey.com/product-detail/en/molex/0430452228/WM10740-ND/3310312
430452428 | 24 | 3.0mm | 3.0mm | 0 | No | Gold | 430452428 | Molex Micro-Fit.SchLib | 430452428 | Molex Micro-Fit.PcbLib | WM10746-ND | https://www.digikey.com/product-detail/en/molex/0430452428/WM10746-ND/3310329

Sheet: Mill-Max
Part Number | Positions | Pitch | Row Spacing | Angle | Flange | Contact | Library Ref | Library Path | Footprint Ref | Footprint Path | Digikey Part Number | Digikey Link
0906-4-15-20 | 1 | NA | NA | 90 | NA | Gold | 0906-4-15-20 | Mill-Max.SchLib | 0906-4-15-20 | Mill-Max.PcbLib | ED8184-ND | https://www.digikey.com/product-detail/en/mill-max-manufacturing-corp/0906-4-15-20-75-14-11-0/ED8184-ND/1147052
0850-0-15-20-83-14-11-0 | 1 | NA | NA | 90 | NA | Gold | 0850-0-15-20-83-14-11-0 | Mill-Max.SchLib | 0850-0-15-20-83-14-11-0 | Mill-Max.PcbLib | ED90436-ND | https://www.digikey.com.au/products/en?keywords=0850-0-15-20-83-14-11-0
 |  |  |  |  |  |  |  |  | c

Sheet: TH 025
Part Number | Positions | Pitch | Row Spacing | Angle | Flange | Contact | Library Ref | Library Path | Footprint Ref | Footprint Path | Digikey Part Number | Digikey Link
1376113-6 | 40 | 3 | 2.2 | 180 | na | Gold | 1376113-6 | TH 025.SchLib | 1376113-6 | TH 025.PcbLib | 1376113-6-ND | https://www.digikey.com.au/products/en?keywords=1376113-6

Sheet: JST
Part Number | Positions | Pitch | Row Spacing | Angle | Flange | Contact | Library Ref | Library Path | Footprint Ref | Footprint Path | Digikey Part Number | Digikey Link
B2B-XH-A(LF)(SN) | 2 | 2.54mm | 2.54mm | 0 | No | Tin | Header 1x2 | JST.SchLib | XH 2 PIN VERT | JST.PcbLib | 455-2247-ND | https://www.digikey.com.au/en/products/detail/jst-sales-america-inc/B2B-XH-A-LF-SN/1651045
 | 3 | 2.54mm | 2.54mm | 0 | No | NA | Header 1x3 | JST.SchLib |  | JST.PcbLib
 | 4 | 2.54mm | 2.54mm | 0 | No | NA | Header 1x4 | JST.SchLib |  | JST.PcbLib
 | 5 | 2.54mm | 2.54mm | 0 | No | NA | Header 1x5 | JST.SchLib |  | JST.PcbLib
 | 6 | 2.54mm | 2.54mm | 0 | No | NA | Header 1x6 | JST.SchLib |  | JST.PcbLib
 | 7 | 2.54mm | 2.54mm | 0 | No | NA | Header 1x7 | JST.SchLib |  | JST.PcbLib
 | 8 | 2.54mm | 2.54mm | 0 | No | NA | Header 1x8 | JST.SchLib |  | JST.PcbLib
 | 9 | 2.54mm | 2.54mm | 0 | No | NA | Header 1x9 | JST.SchLib |  | JST.PcbLib
 | 10 | 2.54mm | 2.54mm | 0 | No | NA | Header 1x10 | JST.SchLib |  | JST.PcbLib

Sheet: Generic
Part Number | Positions | Pitch | Row Spacing | Angle | Flange | Contact | Library Ref | Library Path | Footprint Ref | Footprint Path
TH Test Point | 1 | 0mm | 0mm | 0 | No | NA | Test Point | generic.SchLib | TH Test Point | generic.PcbLib
TH 2.54mm Header 1x2 | 2 | 2.54mm | 2.54mm | 0 | No | NA | Header 1x2 | generic.SchLib | TH 2.54mm Header 1x2 | generic.PcbLib
TH 2.54mm Header 1x3 | 3 | 2.54mm | 2.54mm | 0 | No | NA | Header 1x3 | generic.SchLib | TH 2.54mm Header 1x3 | generic.PcbLib
TH 2.54mm Header 1x4 | 4 | 2.54mm | 2.54mm | 0 | No | NA | Header 1x4 | generic.SchLib | TH 2.54mm Header 1x4 | generic.PcbLib
TH 2.54mm Header 1x5 | 5 | 2.54mm | 2.54mm | 0 | No | NA | Header 1x5 | generic.SchLib | TH 2.54mm Header 1x5 | generic.PcbLib
TH 2.54mm Header 1x6 | 6 | 2.54mm | 2.54mm | 0 | No | NA | Header 1x6 | generic.SchLib | TH 2.54mm Header 1x6 | generic.PcbLib
TH 2.54mm Header 1x7 | 7 | 2.54mm | 2.54mm | 0 | No | NA | Header 1x7 | generic.SchLib | TH 2.54mm Header 1x7 | generic.PcbLib
TH 2.54mm Header 1x8 | 8 | 2.54mm | 2.54mm | 0 | No | NA | Header 1x8 | generic.SchLib | TH 2.54mm Header 1x8 | generic.PcbLib
TH 2.54mm Header 1x9 | 9 | 2.54mm | 2.54mm | 0 | No | NA | Header 1x9 | generic.SchLib | TH 2.54mm Header 1x9 | generic.PcbLib
TH 2.54mm Header 1x10 | 10 | 2.54mm | 2.54mm | 0 | No | NA | Header 1x10 | generic.SchLib | TH 2.54mm Header 1x10 | generic.PcbLib
TH 2.54mm Header 2x2 | 4 | 2.54mm | 2.54mm | 0 | No | NA | Header 2x2 | generic.SchLib | TH 2.54mm Header 2x2 | generic.PcbLib
TH 2.54mm Header 2x3 | 6 | 2.54mm | 2.54mm | 0 | No | NA | Header 2x3 | generic.SchLib | TH 2.54mm Header 2x3 | generic.PcbLib
TH 2.54mm Header 2x4 | 8 | 2.54mm | 2.54mm | 0 | No | NA | Header 2x4 | generic.SchLib | TH 2.54mm Header 2x4 | generic.PcbLib
TH 2.54mm Header 2x5 | 10 | 2.54mm | 2.54mm | 0 | No | NA | Header 2x5 | generic.SchLib | TH 2.54mm Header 2x5 | generic.PcbLib
TH 2.54mm Header 2x6 | 12 | 2.54mm | 2.54mm | 0 | No | NA | Header 2x6 | generic.SchLib | TH 2.54mm Header 2x6 | generic.PcbLib
TH 2.54mm Header 2x7 | 14 | 2.54mm | 2.54mm | 0 | No | NA | Header 2x7 | generic.SchLib | TH 2.54mm Header 2x7 | generic.PcbLib
TH 2.54mm Header 2x8 | 16 | 2.54mm | 2.54mm | 0 | No | NA | Header 2x8 | generic.SchLib | TH 2.54mm Header 2x8 | generic.PcbLib
TH 2.54mm Header 2x9 | 18 | 2.54mm | 2.54mm | 0 | No | NA | Header 2x9 | generic.SchLib | TH 2.54mm Header 2x9 | generic.PcbLib
TH 2.54mm Header 2x10 | 20 | 2.54mm | 2.54mm | 0 | No | NA | Header 2x10 | generic.SchLib | TH 2.54mm Header 2x10 | generic.PcbLib
TH 2.54mm Header 2x11 | 20 | 2.54mm | 2.54mm | 0 | No | NA | Header 1x16 | generic.SchLib | TH 2.54mm Header 2x11 | generic.PcbLib
TH 2.54mm Header 2x12 | 20 | 2.54mm | 2.54mm | 0 | No | NA | Header 1x20 | generic.SchLib | TH 2.54mm Header 2x12 | generic.PcbLib
TH 5.08mm Header 1x2 | 2 | 2.54mm | 5.08mm | 0 | No | NA | Header 1x2 | generic.SchLib | TH 5.08mm Header 1x2 | generic.PcbLib
TH 5.08mm Header 1x3 | 3 | 2.54mm | 5.08mm | 0 | No | NA | Header 1x3 | generic.SchLib | TH 5.08mm Header 1x3 | generic.PcbLib
TH 5.08mm Header 1x4 | 4 | 2.54mm | 5.08mm | 0 | No | NA | Header 1x4 | generic.SchLib | TH 5.08mm Header 1x4 | generic.PcbLib
SMD Test Point | 1 | 0mm | 0 | 0 | No | NA | Test Point | generic.SchLib | SMD Test Point | generic.PcbLib
SMD Test Point Small | 1 | 0mm | 0 | 0 | No | NA | Test Point Small | generic.SchLib | SMD Test Point 1mm | generic.PcbLib

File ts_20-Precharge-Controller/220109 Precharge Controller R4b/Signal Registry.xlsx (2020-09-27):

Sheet: Precharge
 | Power | Input Signals |  |  | Output Signals |  |  | Taps |  |  | High-Speed Busses
Type | Name | Input Source | Name | Signal Type | Output Source | Name | Signal Sype | Source | Name | Signal Sype
 | GLV+ |  | IMD Data | Digital |  | Heartbeat | Int |  |  |  | I2C SDA (ISO) | Digital
 | 5V |  | IMD OK | Digital |  | State | Int |  |  |  | I2C SCL (ISO) | Digital
 | 5V (ISO) |  | MC Voltage | Analogue |  |  |  |  |  |  | I2C SDA (MC) | Digital
 | 3.3V (ISO) |  | Battery Voltage | Analogue |  |  |  |  |  |  | I2C SCL (MC) | Digital
 | 5V (CAN) | CAN (Throttle) | Precharge Button | Digital |  |  |  |  |  |  | I2C SDA (Battery) | Digital
 | 5V (MC) |  | AIR+ FB | Digital |  |  |  |  |  |  | I2C SCL (Battery) | Digital
 | 5V (Battery) |  | AIR- FB | Digital |  |  |  |  |  |  | I2C SDA (PDOC) | Digital
 | 5V (PDOC) | CAN (Orion) | AMS OK | Digital |  |  |  |  |  |  | I2C SCL (PDOC) | Digital
 | AIR Power |  |  |  |  |  |  |  |  |  | CAN TX | Digital
 | Green In |  |  |  |  |  |  |  |  |  | CAN RX | Digital
 | Green Out

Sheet: Virtual Dashboard
Input |  | Output
Precharge Button | Digital | Heartbeat | Int (8)
Orion OK | Digital | State | Int (8)
 |  | pdoc temperature | int (16)
 |  | pdof reference temp | Int 16
 |  | mc voltage | int 16
 |  | battery voltage | int 16
 |  | error present | digital
 |  | error code | int 8
 |  | warning present | digital
 |  | warning code | int 8
 |  | pdoc ok | digital
 |  | imd ok | digital
 |  | air power | digital
 |  | air negative feedback | digital
 |  | air positive feedback | digital

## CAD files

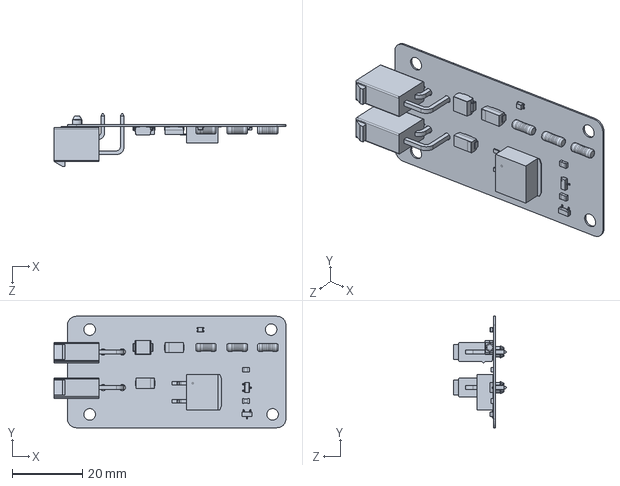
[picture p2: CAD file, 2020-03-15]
ts_20-Accumulator-Active-Indicator/160320 AAI R1/AAI.SLDPRT
66.0 x 31.8 x 15.0 mm

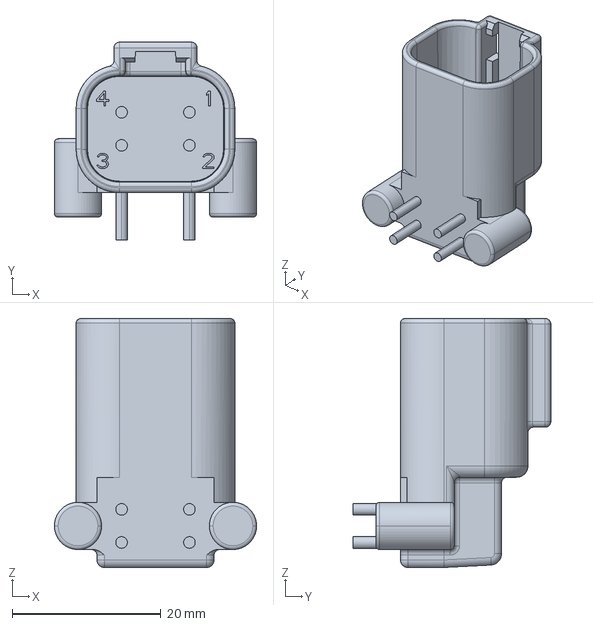
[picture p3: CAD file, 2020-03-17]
~ts_20 Library/ts_20-standard-connectors/DT/cad/c-dtf13-4p-a-3d.stp
27.2 x 26.6 x 33.5 mm

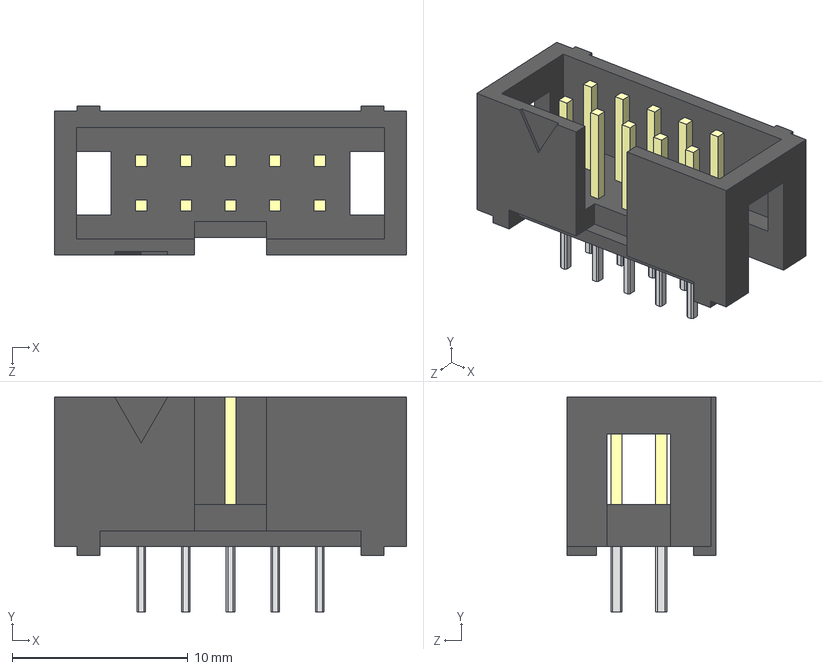
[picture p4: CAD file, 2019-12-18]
~ts_20 Library/ts_20-standard-connectors/Generic/XG4C_1031.step
20.0 x 12.2 x 8.50 mm

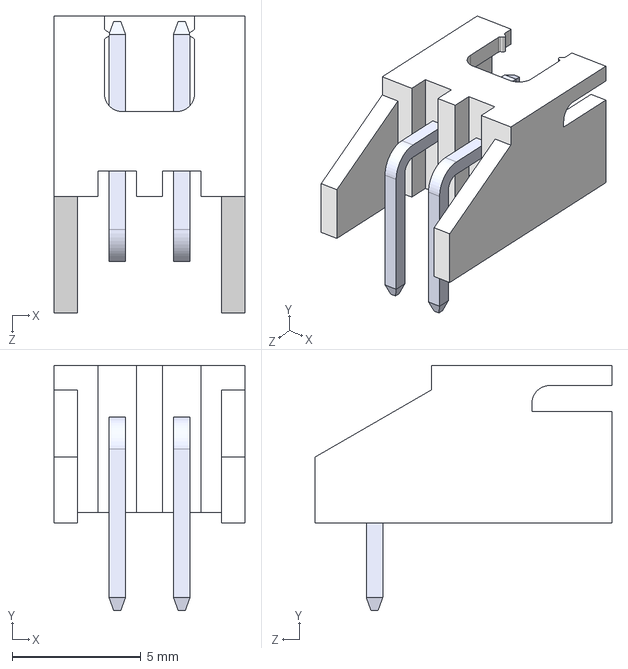
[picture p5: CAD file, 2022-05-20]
~ts_20 Library/ts_20-standard-connectors/JST/cad/JST - XH - Thru V - 2.54mm/S2B-XH-A-LF--SN---3DModel-STEP-1.STEP
7.40 x 9.50 x 11.5 mm

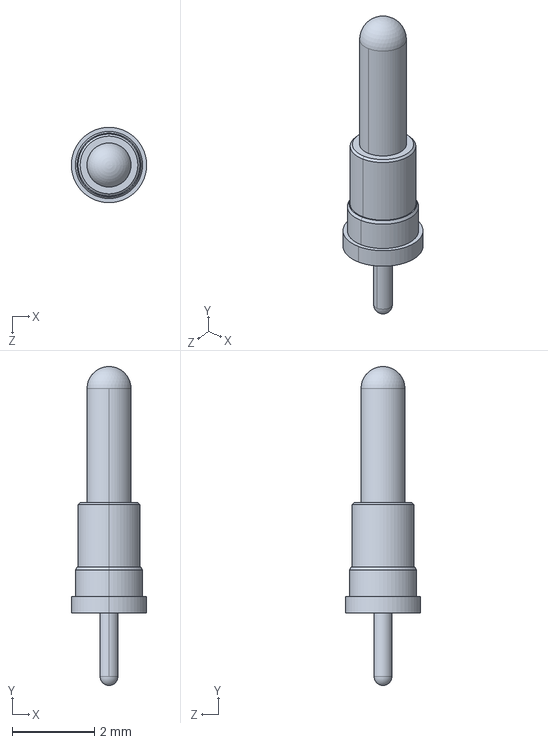
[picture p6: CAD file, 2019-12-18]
~ts_20 Library/ts_20-standard-connectors/Mill-Max/cad/0906-4-15-20.STEP
1.83 x 7.75 x 1.83 mm

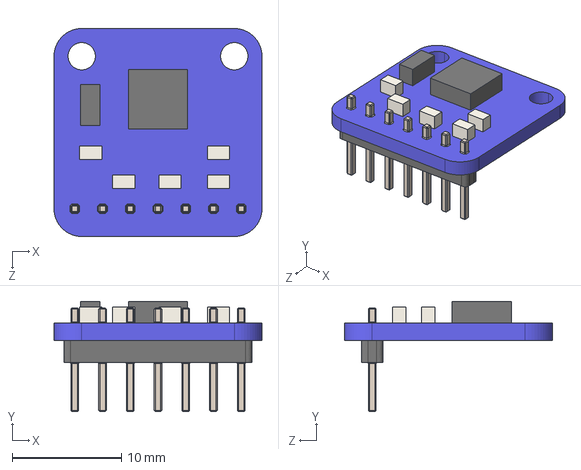
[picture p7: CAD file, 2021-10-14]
~ts_20 Library/ts_20-standard-library/cad/Adafruit Accelerometer PCB.STEP
19.1 x 10.1 x 19.0 mm

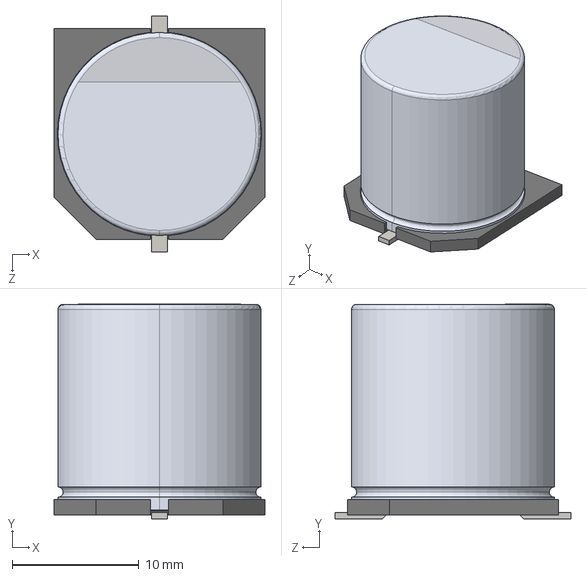
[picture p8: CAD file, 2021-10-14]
~ts_20 Library/ts_20-standard-library/cad/aluminium_caps/vishay 1616.STEP
16.6 x 16.9 x 18.6 mm

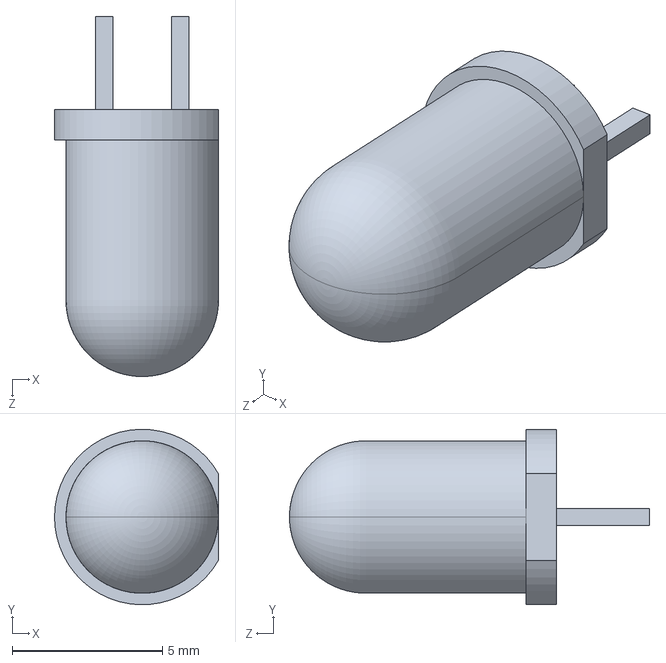
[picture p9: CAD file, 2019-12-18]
~ts_20 Library/ts_20-standard-library/cad/sldwrks/5MM LED SMALL.SLDPRT
5.46 x 5.84 x 12.0 mm

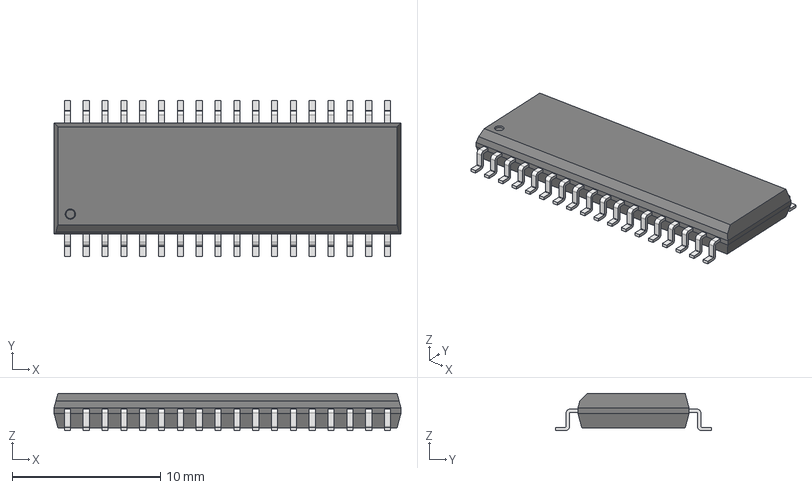
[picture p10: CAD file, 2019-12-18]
~ts_20 Library/ts_20-standard-library/cad/SO_package/S036W.stp
23.4 x 10.5 x 2.50 mm

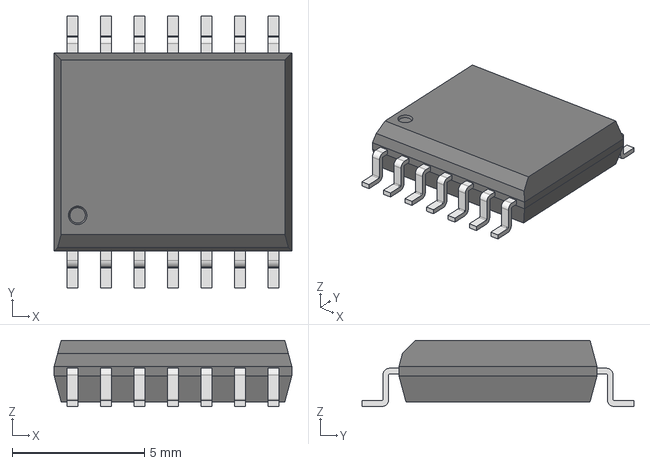
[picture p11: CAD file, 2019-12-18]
~ts_20 Library/ts_20-standard-library/cad/soic-package-collection-1.snapshot.6/SO_package/S014W.stp
9.00 x 10.3 x 2.50 mm

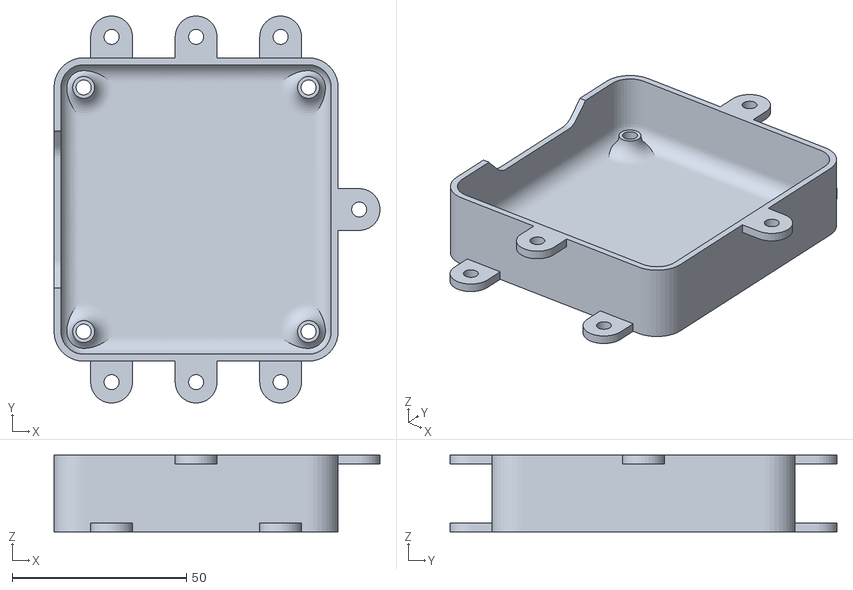
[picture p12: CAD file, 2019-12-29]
ts_20-BSPD-Current-Sensor/200421 BSPD Current Detector R2/Enclosure/Bottom.STL
93.5 x 111.0 x 22.0

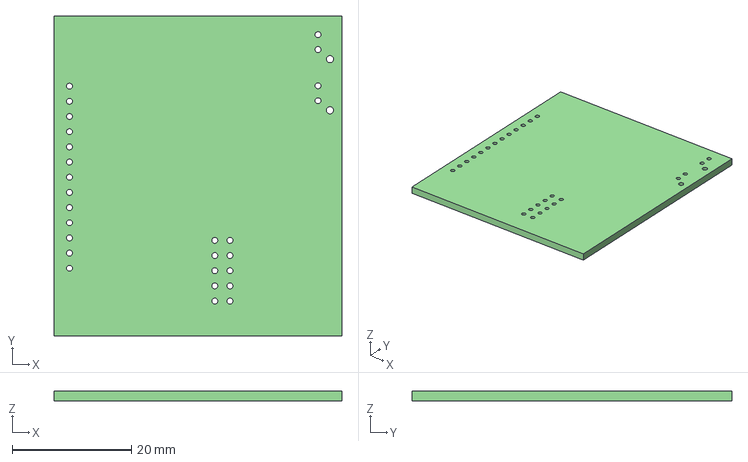
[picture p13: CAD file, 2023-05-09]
ts_23_BMS_SLAVE/LVBMS_A_Sample_R2/LVBMS_A_Sample_R2.step
48.2 x 53.5 x 1.60 mm

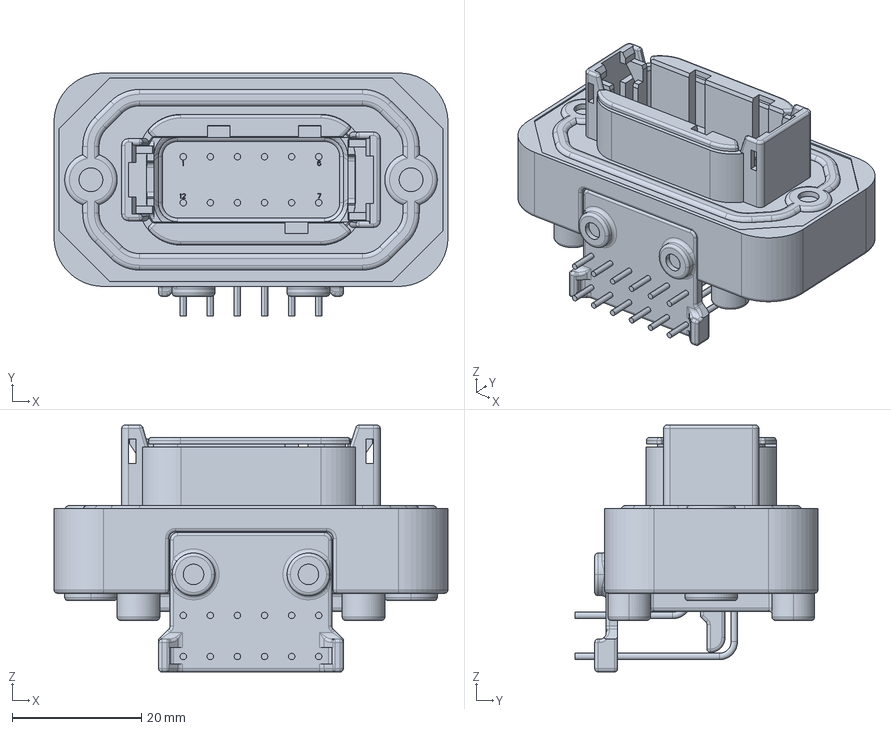
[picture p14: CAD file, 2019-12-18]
~ts_20 Library/ts_20-standard-connectors/cad/c-dtm13-12pa-99-3d.stp
61.0 x 37.6 x 38.2 mm

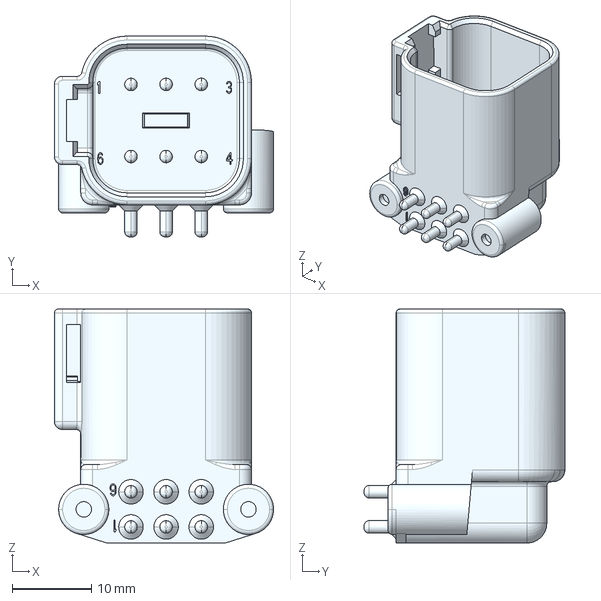
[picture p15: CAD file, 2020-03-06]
~ts_20 Library/ts_20-standard-connectors/DT/cad/c-dtf13-6p-99-3d.stp
27.7 x 25.4 x 29.6 mm

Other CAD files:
ts_20-BSPD-Current-Sensor/200421 BSPD Current Detector R2/Enclosure/Part4.sldprt
ts_20_Autonomous-Terminal-Board/Autonomous Terminal Board/terminal_board_pcb v4.wrl.SLDPRT
ts_23_BMS_SLAVE/LVBMS_A_Sample_R2/LVBMS_A_Sample_R2 PCB.step.SLDPRT
~ts_20 Library/ts_20-standard-connectors/DT/cad/c-dt13-12pa-b016-99-3d.stp
~ts_20 Library/ts_20-standard-connectors/DT/cad/c-dt13-4p-c-3d.stp
~ts_20 Library/ts_20-standard-connectors/DT/cad/c-dt13-6p-99-3d.stp
~ts_20 Library/ts_20-standard-connectors/DT/cad/c-dt15-12pa-b016-99-3d.stp
~ts_20 Library/ts_20-standard-connectors/DT/cad/c-dt15-6p-99-3d.stp
~ts_20 Library/ts_20-standard-connectors/DT/cad/c-dtf13-12pa-99-3d.stp
~ts_20 Library/ts_20-standard-connectors/JST/cad/JST - XH - Thru V - 2.54mm/JST - XH - Thru V - 10Pin - 2.54mm.stp
~ts_20 Library/ts_20-standard-connectors/JST/cad/JST - XH - Thru V - 2.54mm/JST - XH - Thru V - 11Pin - 2.54mm.stp
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

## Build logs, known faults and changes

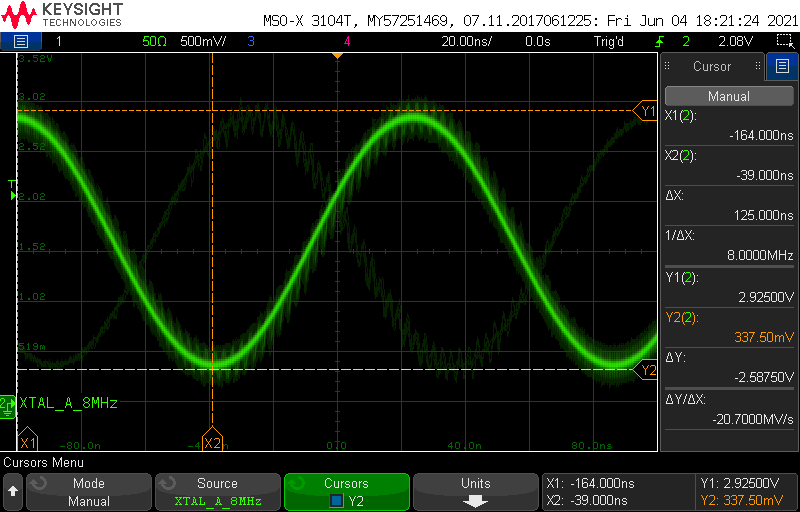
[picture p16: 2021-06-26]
ts_20-Precharge-Controller/220109 Precharge Controller R4b/Crystal Failure Captures/scope_22.png

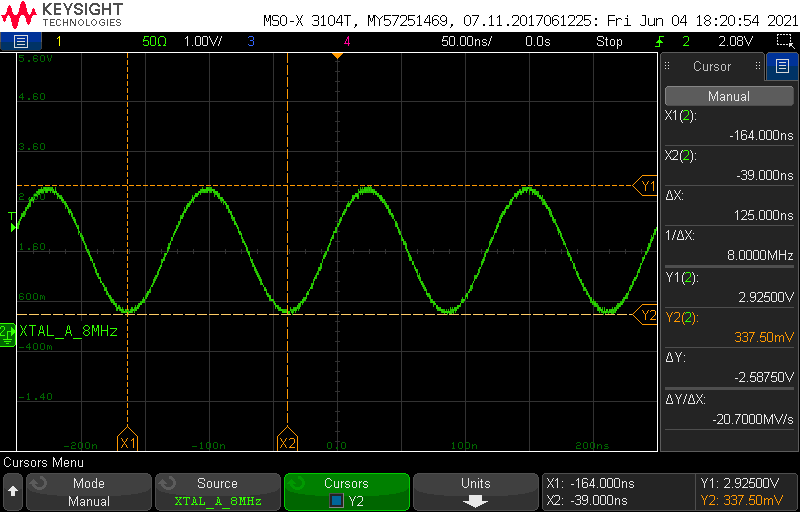
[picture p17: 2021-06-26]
ts_20-Precharge-Controller/220109 Precharge Controller R4b/Crystal Failure Captures/scope_21.png

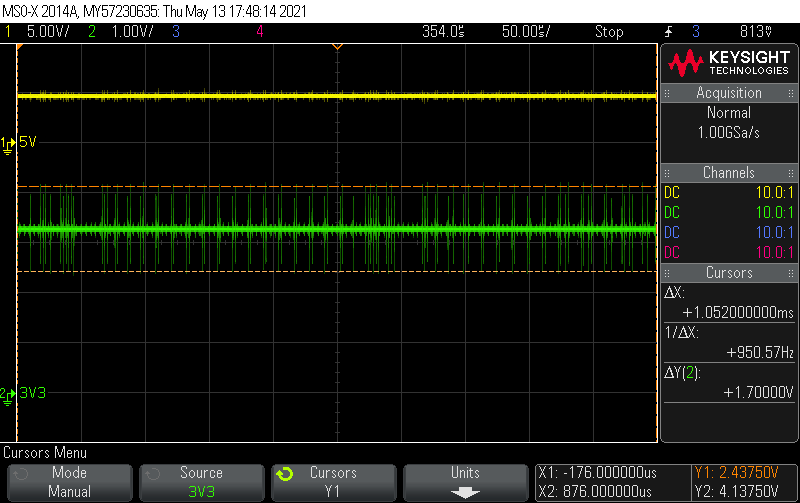
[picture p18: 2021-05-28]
ts_20-Precharge-Controller/220109 Precharge Controller R4b/CANBUS Failure Captures/scope_17.png

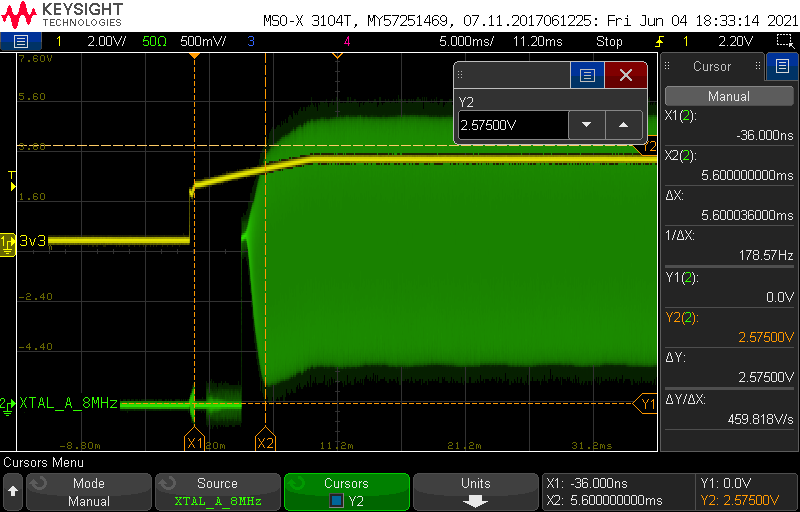
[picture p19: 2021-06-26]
ts_20-Precharge-Controller/220109 Precharge Controller R4b/Crystal Failure Captures/scope_25.png

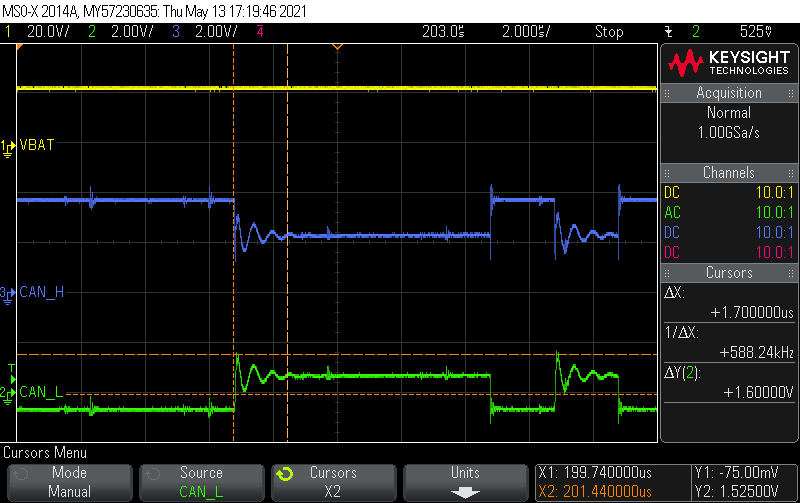
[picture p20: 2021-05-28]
ts_20-Precharge-Controller/220109 Precharge Controller R4b/CANBUS Failure Captures/scope_0.png

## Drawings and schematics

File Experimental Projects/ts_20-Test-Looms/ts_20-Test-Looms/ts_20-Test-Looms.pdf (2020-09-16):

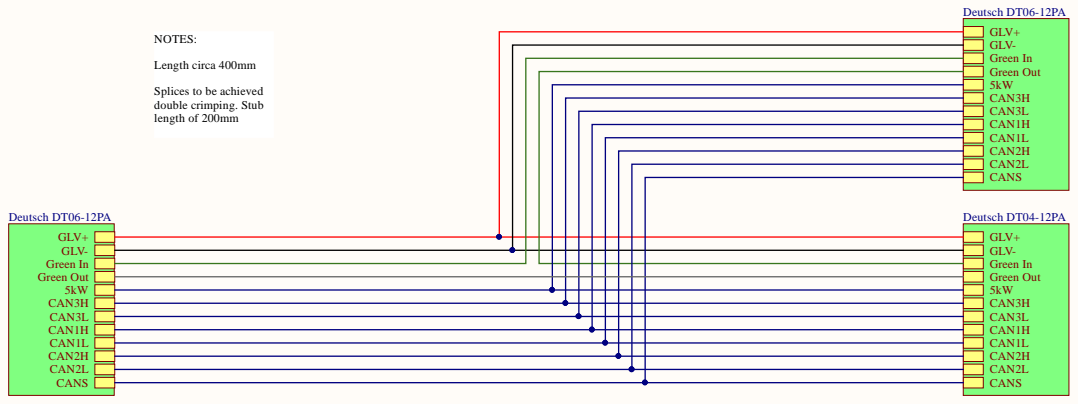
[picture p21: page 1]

Splices to be achieved
double crimping. Stub
length of 200mm

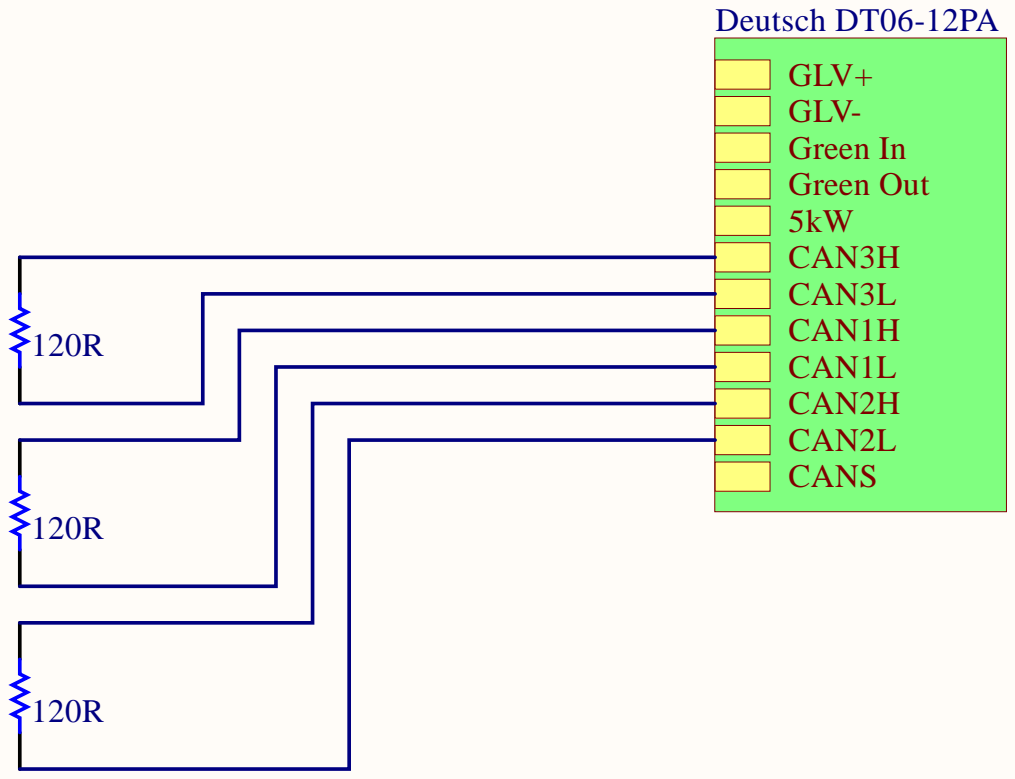
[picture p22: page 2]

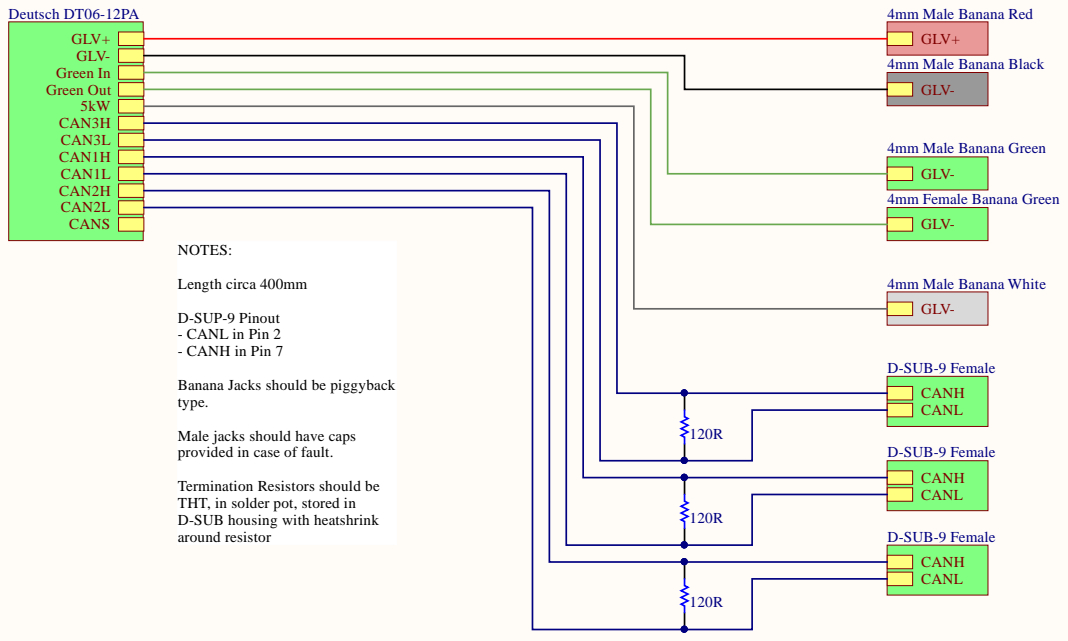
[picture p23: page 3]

4mm Male Banana Red GLV- 4mm Male Banana Black

4mm Male Banana Green GLV- 4mm Female Banana Green GLV- 4mm Male Banana White

D-SUP-9 Pi n o u t - CA N L i n Pi n 2 - CA N H i n Pi n 7 Banana Jack s s h o u l d be p i g g y back

t y pe. Male jack s s h o u l d have cap s pro v i ded i n case of fau l t .

Termi nat i o n Res i s t ors s h o u l d be T H T, i n s o l der p o t, s t ored i n D-SUB h o u s i n g w i t h heat s hri n k aro u n d res i s t o r

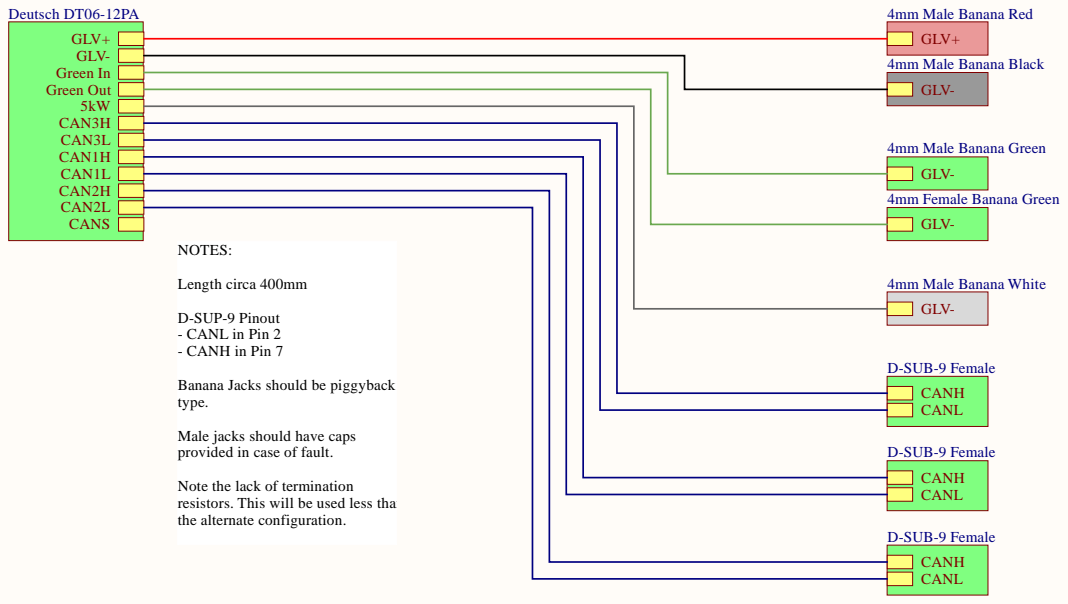
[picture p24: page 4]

D-SUP-9 Pinout - CANL in Pin 2 - CANH in Pin 7 Banana Jacks should be piggyback

type.

Male jacks should have caps provided in case of fault.

Note the lack of termination
resistors. This will be used less than the alternate configuration.

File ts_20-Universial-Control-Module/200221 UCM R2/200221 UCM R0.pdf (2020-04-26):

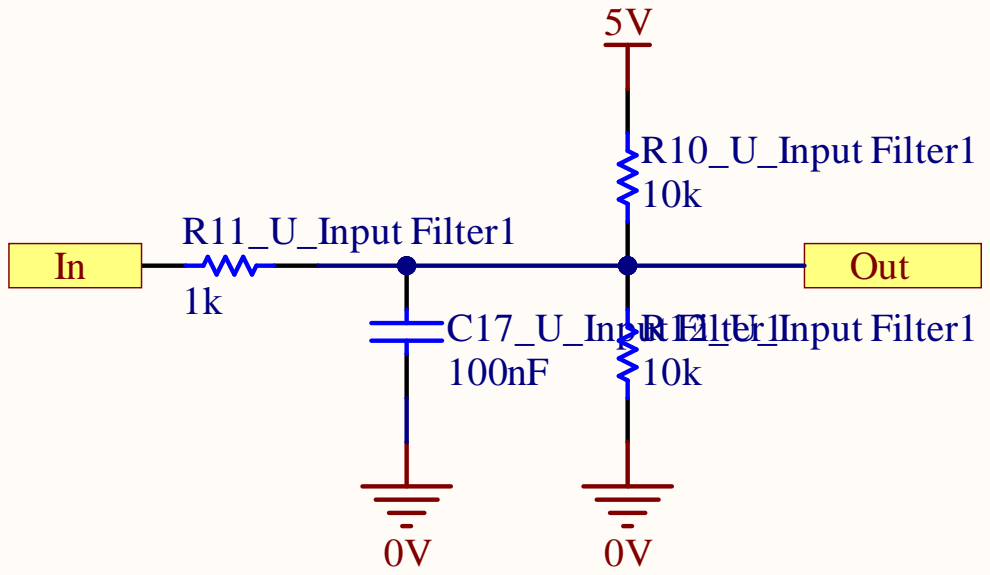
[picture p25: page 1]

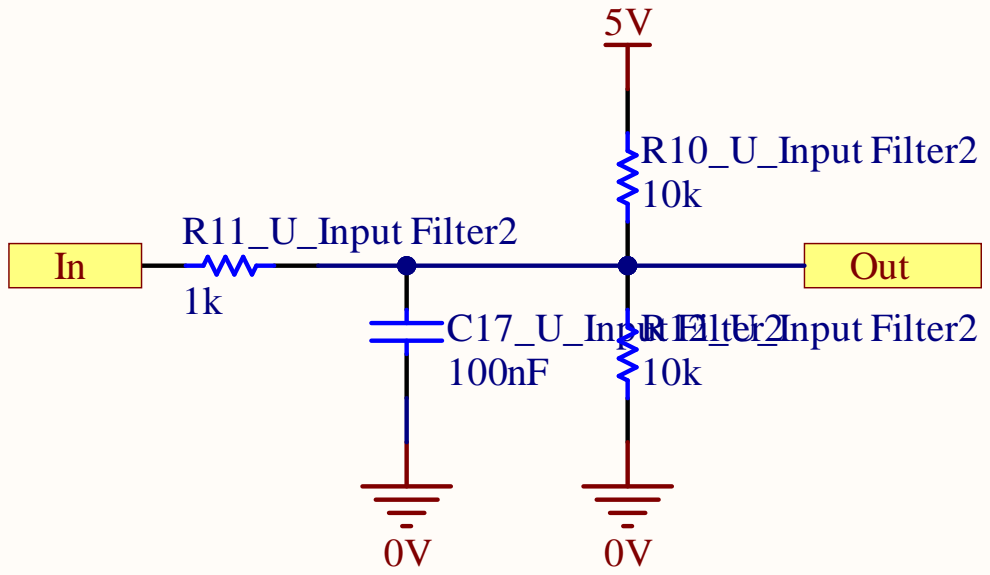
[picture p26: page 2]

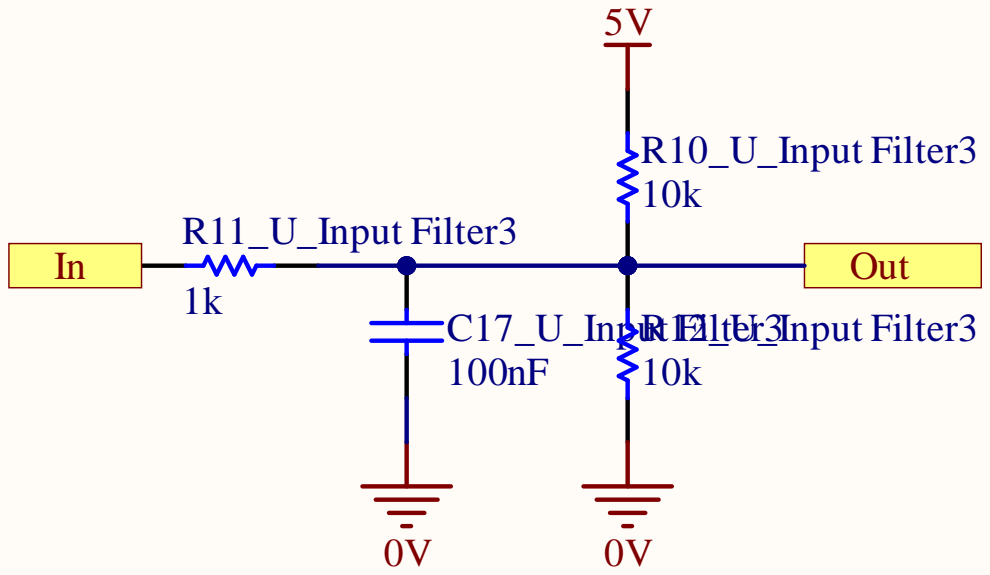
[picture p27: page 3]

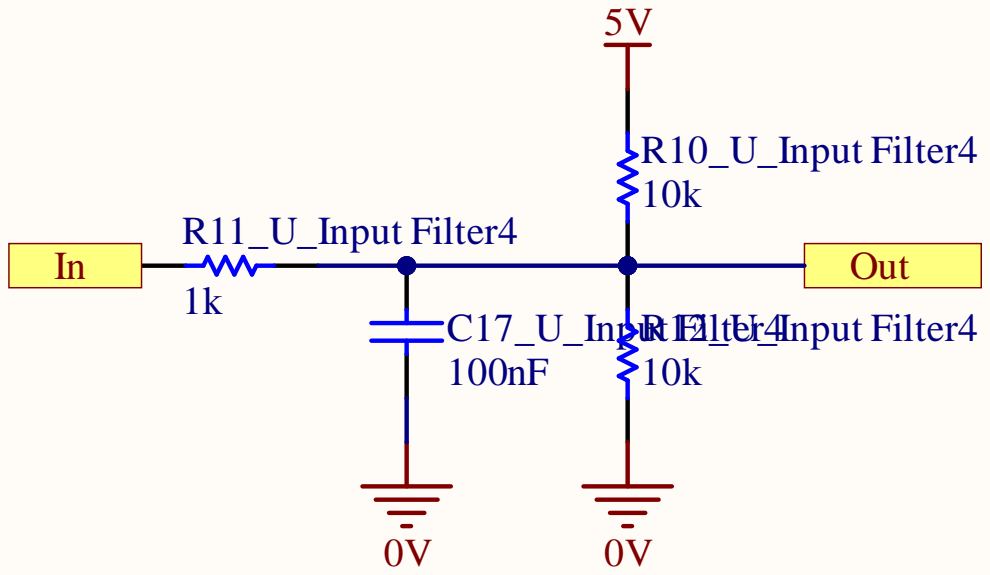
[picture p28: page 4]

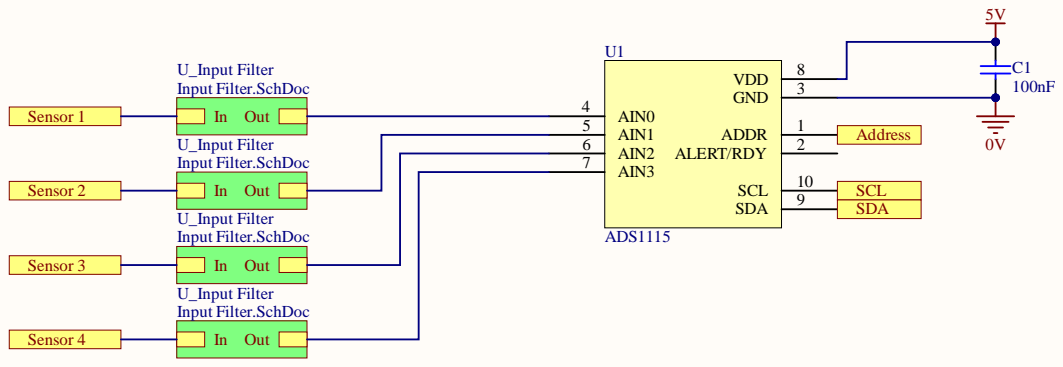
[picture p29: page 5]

AIN1 5
AIN2 6
AIN3 7

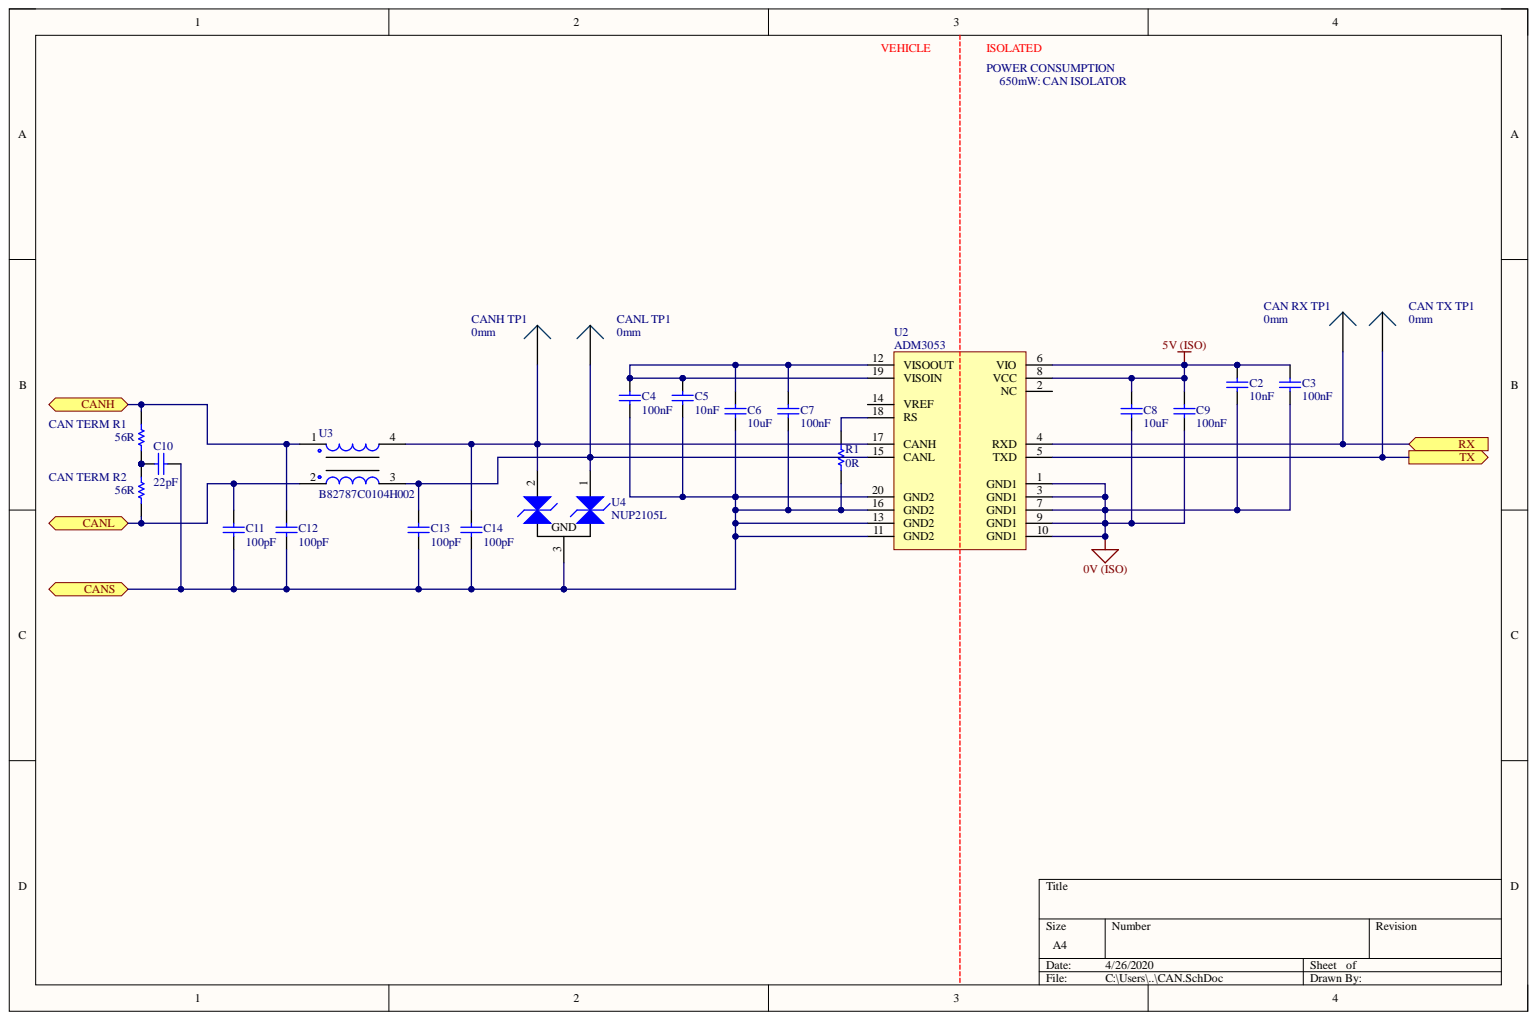
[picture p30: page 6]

VREF 14

10uF | CANH 17 CANL 15

0R | GND2 20

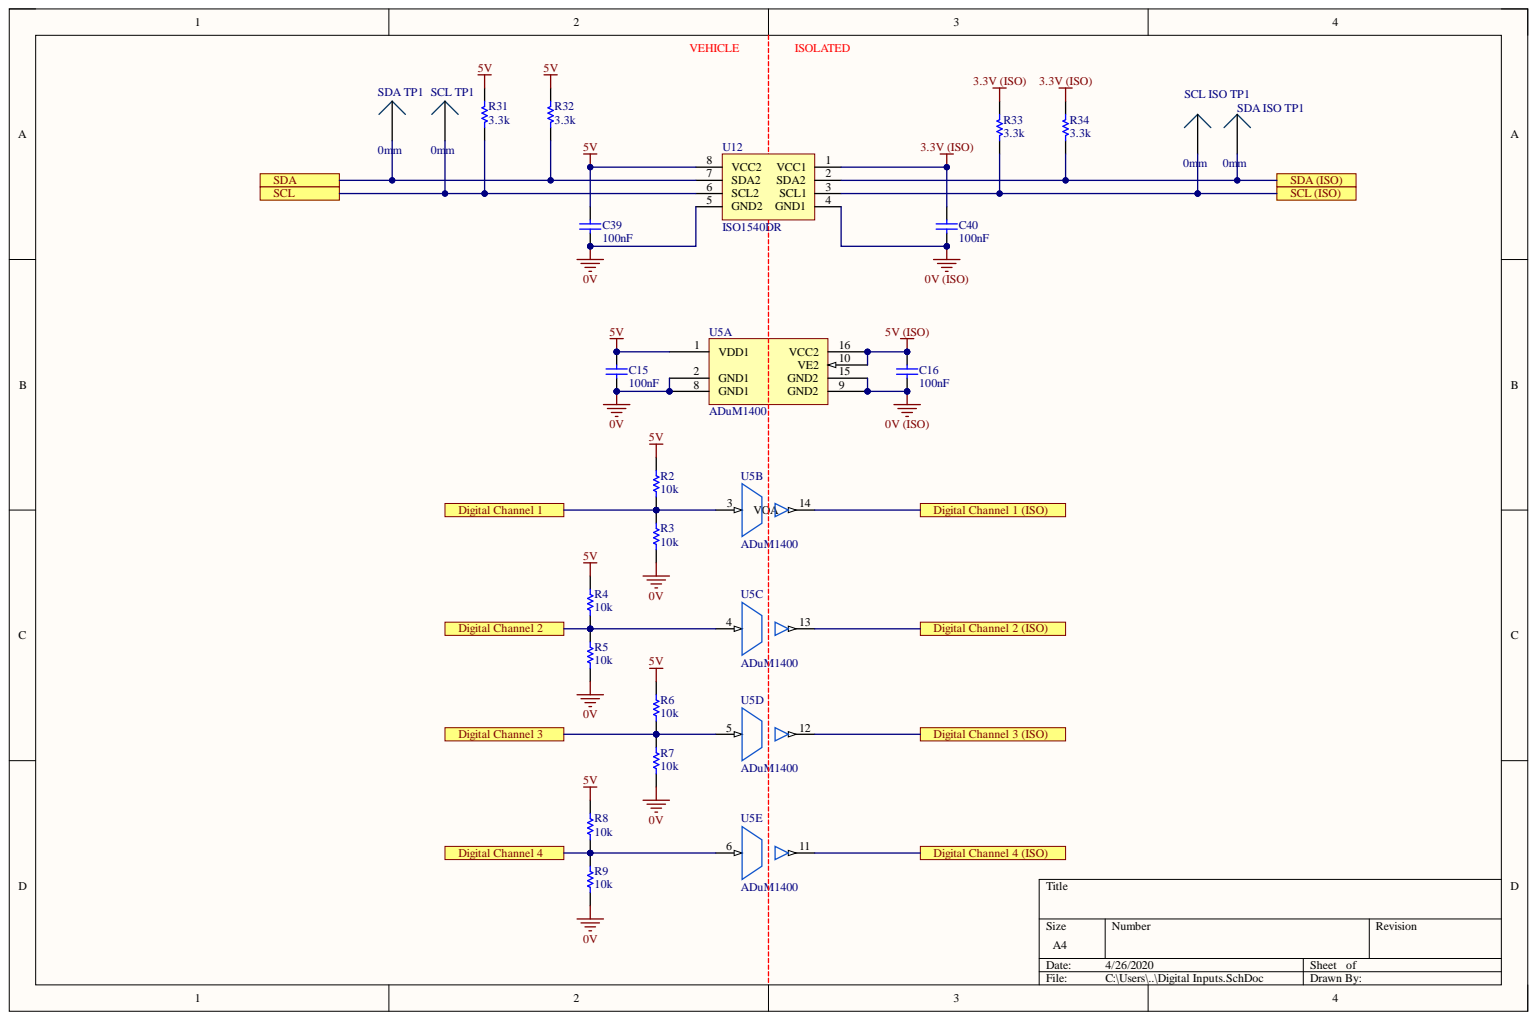
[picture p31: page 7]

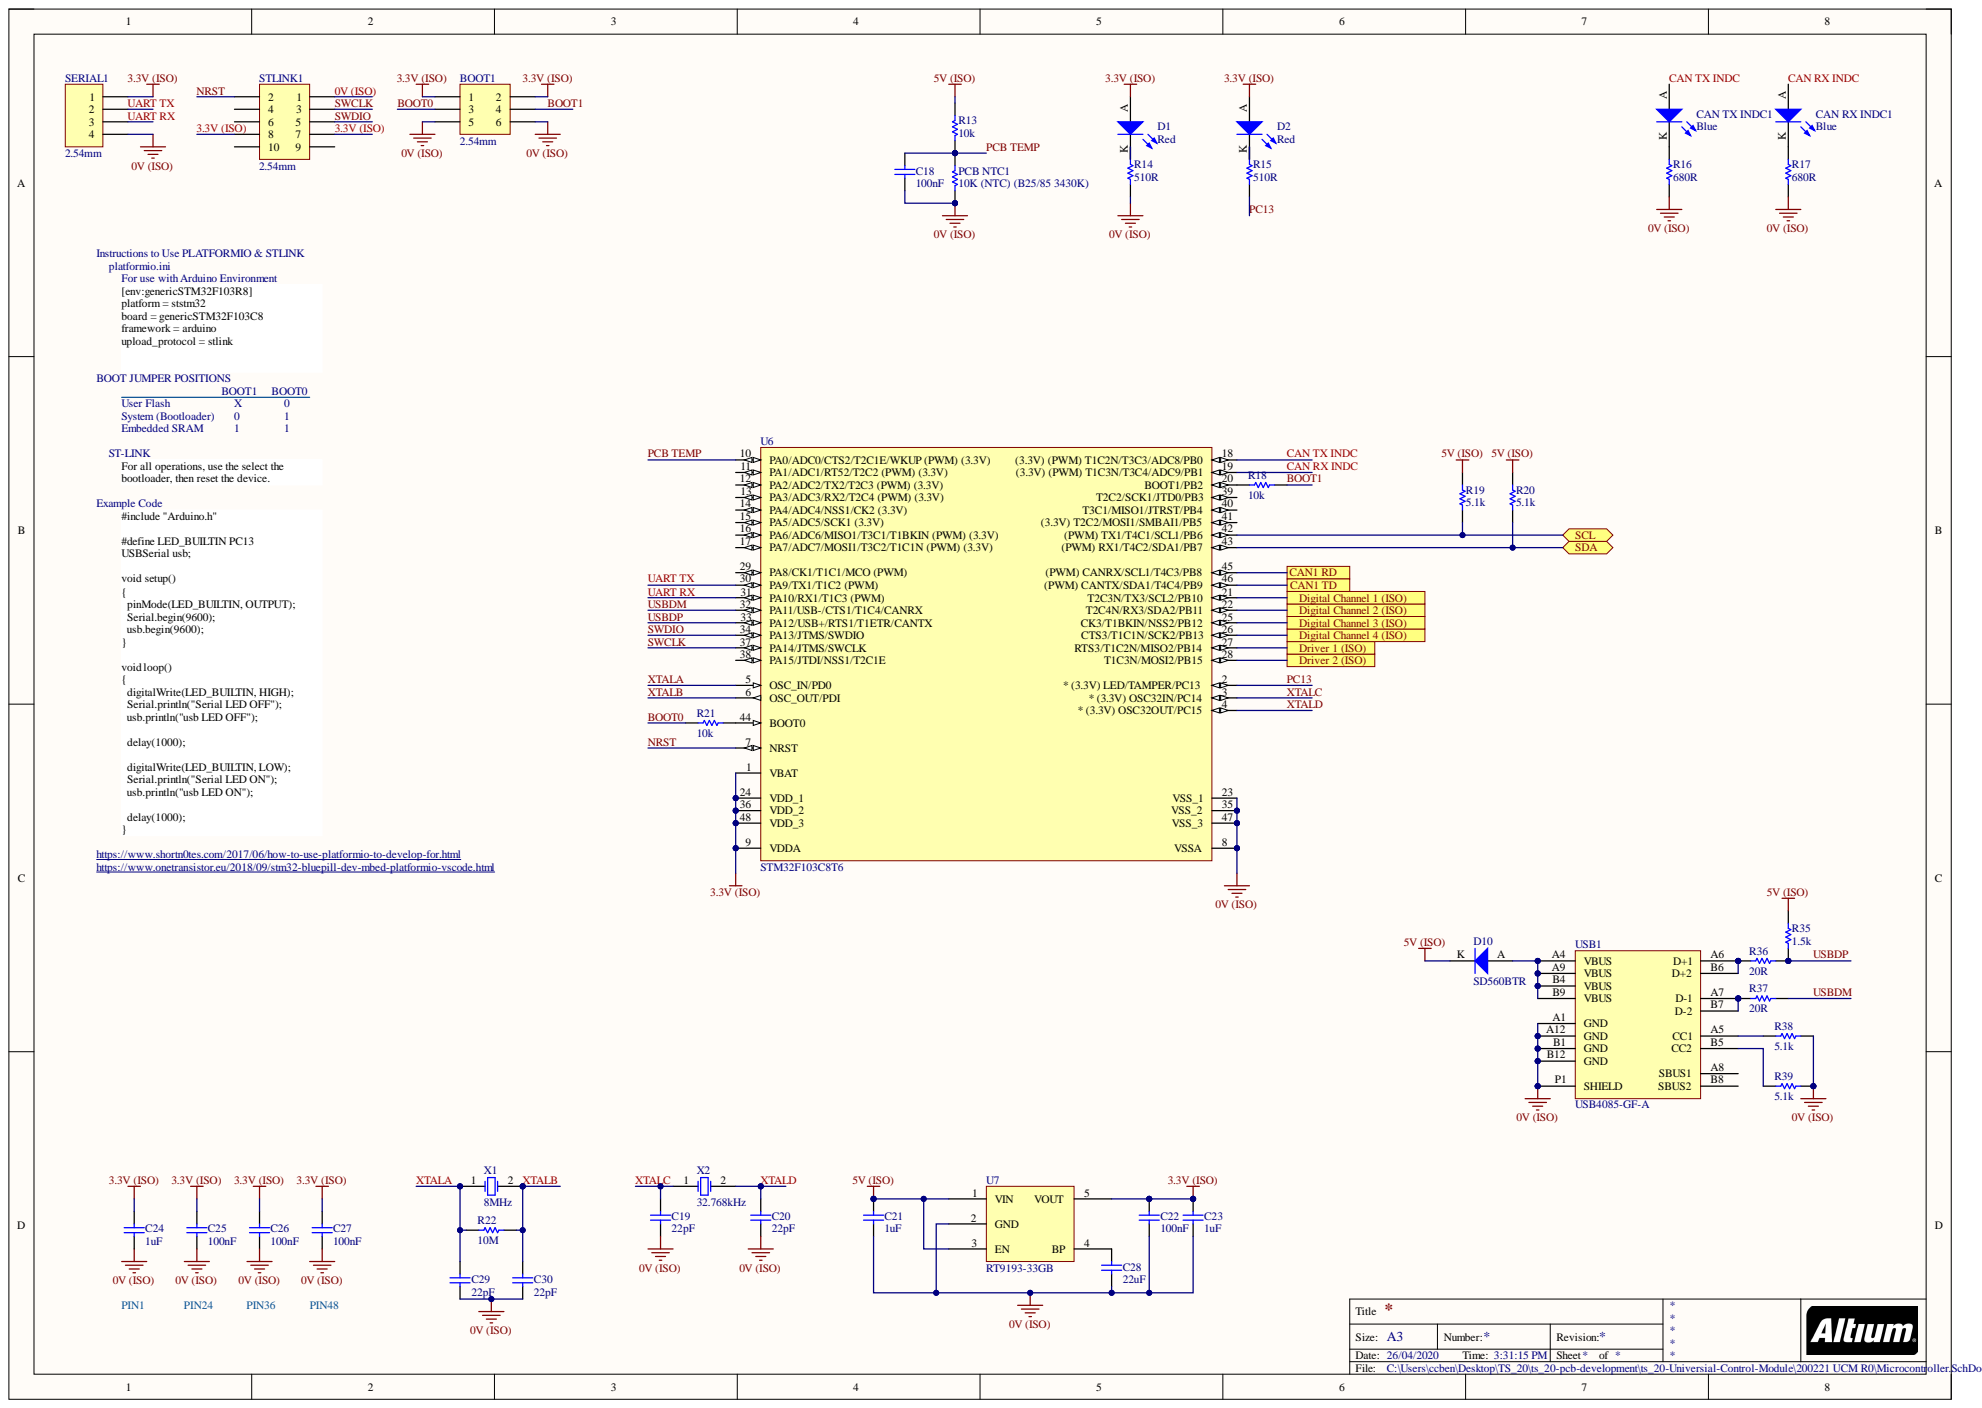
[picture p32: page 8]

Instructions to Use PLATFORMIO & STLINK
platformio.ini
For use with Arduino Environment
[env:genericSTM32F103R8]
platform = ststm32
board = genericSTM32F103C8
framework = arduino
upload_protocol = stlink

ST-LINK
For all operations, use the select the
bootloader, then reset the device.

void loop()
digitalWrite(LED_BUILTIN, HIGH);
Serial.println("Serial LED OFF");
usb.println("usb LED OFF");

OSC_IN/PD0 5 OSC_OUT/PDI 6 BOOT0 44 NRST 7 VBAT 1 | Driver 2 (ISO)

digitalWrite(LED_BUILTIN, LOW);
Serial.println("Serial LED ON");
usb.println("usb LED ON");

https://www.shortn0tes.com/2017/06/how-to-use-platformio-to-develop-for.html
https://www.onetransistor.eu/2018/09/stm32-bluepill-dev-mbed-platformio-vscode.html

C21 | GND 2

C:\Users\ccben\Desktop\TS_20\ts_20-pcb-development\ts_20-Universial-Control-Module\200221 UCM R0\Microcontroller.SchDoc





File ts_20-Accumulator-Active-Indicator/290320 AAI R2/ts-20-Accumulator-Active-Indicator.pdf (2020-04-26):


https://www.edn.com/design/analog/4363797/Circuit-achieves-constant-current-over-wide-range-of-terminal-voltages

Consider the ititial state; above 58V,
current will flow through R57-59, and the
combined V_CE drop across Q9-10 will be
the voltage at the gate. The FET will be on.

D4 functions simply to limit the
voltage at the gate of the MOSFET
to a sensible level.

If there is current is flowing, this implies a
voltage drop across R61. This voltage drop
will block drop the votlage at the gate to 0.

At this point, we return to the initial state,
where there is no current flowing through
the FET, so the SCR will have a voltage
drop across it, and current will flow through
the FET and LED, which turns it off, etc

Q2 & Q3 function as an SCR (Silicon
Controlled Rectifier). R60 essentially
does nothing, however ensures that its
default state is active.

R5 Limits the current
through the gate. It is not the
primary source of limitation
however since the FET is in
constant current mode,
however will affect this.

This holds the voltage at the gate around
3.4V, a where the current is determined by


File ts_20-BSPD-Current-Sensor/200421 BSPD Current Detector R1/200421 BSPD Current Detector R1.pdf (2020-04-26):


DHABS/100 Dual Channel Current Sensor

SDN header included for strain relief purposes.

Feedback Resistor to Reduce output chattering


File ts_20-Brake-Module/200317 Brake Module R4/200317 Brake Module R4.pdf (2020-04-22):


1THRES 2

1RESET 4

Trig/Thres | | 1TRIG 6

BSPD OK


VREF 14

10uF | CANH 17 CANL 15

0R | GND2 20



Connected to 5kW current sensor.


Instructions to Use PLATFORMIO & STLINK
platformio.ini
For use with Arduino Environment
[env:genericSTM32F103R8]
platform = ststm32
board = genericSTM32F103C8
framework = arduino
upload_protocol = stlink

ST-LINK
For all operations, use the select the
bootloader, then reset the device.

BSPD OK (ISO) | PA10/RX1/T1C3 (PWM) 31 | CAN1 TD

#include "Arduino.h" #define LED_BUILTIN PC13 USBSerial usb; void setup() { pinMode(LED_BUILTIN, OUTPUT); Serial.begin(9600); usb.begin(9600); } void loop() { digitalWrite(LED_BUILTIN, HIGH); Serial.println("Serial LED OFF"); usb.println("usb LED OFF"); delay(1000); digitalWrite(LED_BUILTIN, LOW); Serial.println("Serial LED ON"); usb.println("usb LED ON"); delay(1000); } | PA11/USB-/CTS1/T1C4/CANRX 32

https://www.shortn0tes.com/2017/06/how-to-use-platformio-to-develop-for.html
https://www.onetransistor.eu/2018/09/stm32-bluepill-dev-mbed-platformio-vscode.html

C49 | GND 2

C:\Users\ccben\Desktop\TS_20\ts_20-pcb-development\ts_20-Brake-Module\200317 Brake Module R4\Microcontroller.SchDoc



*PULLED LOW AT GATE

*PULLED LOW AT THE 556 TIMER


Sensor: SICK PBT-RB025SG2SS0VMC0Z
https://www.sick.com/au/en/fluid-sensors/pressure-sensors/pbt/pbt-rb025sg2ss0vmc0z/p/p173399

Set BSE brake signal to 75% of reference.








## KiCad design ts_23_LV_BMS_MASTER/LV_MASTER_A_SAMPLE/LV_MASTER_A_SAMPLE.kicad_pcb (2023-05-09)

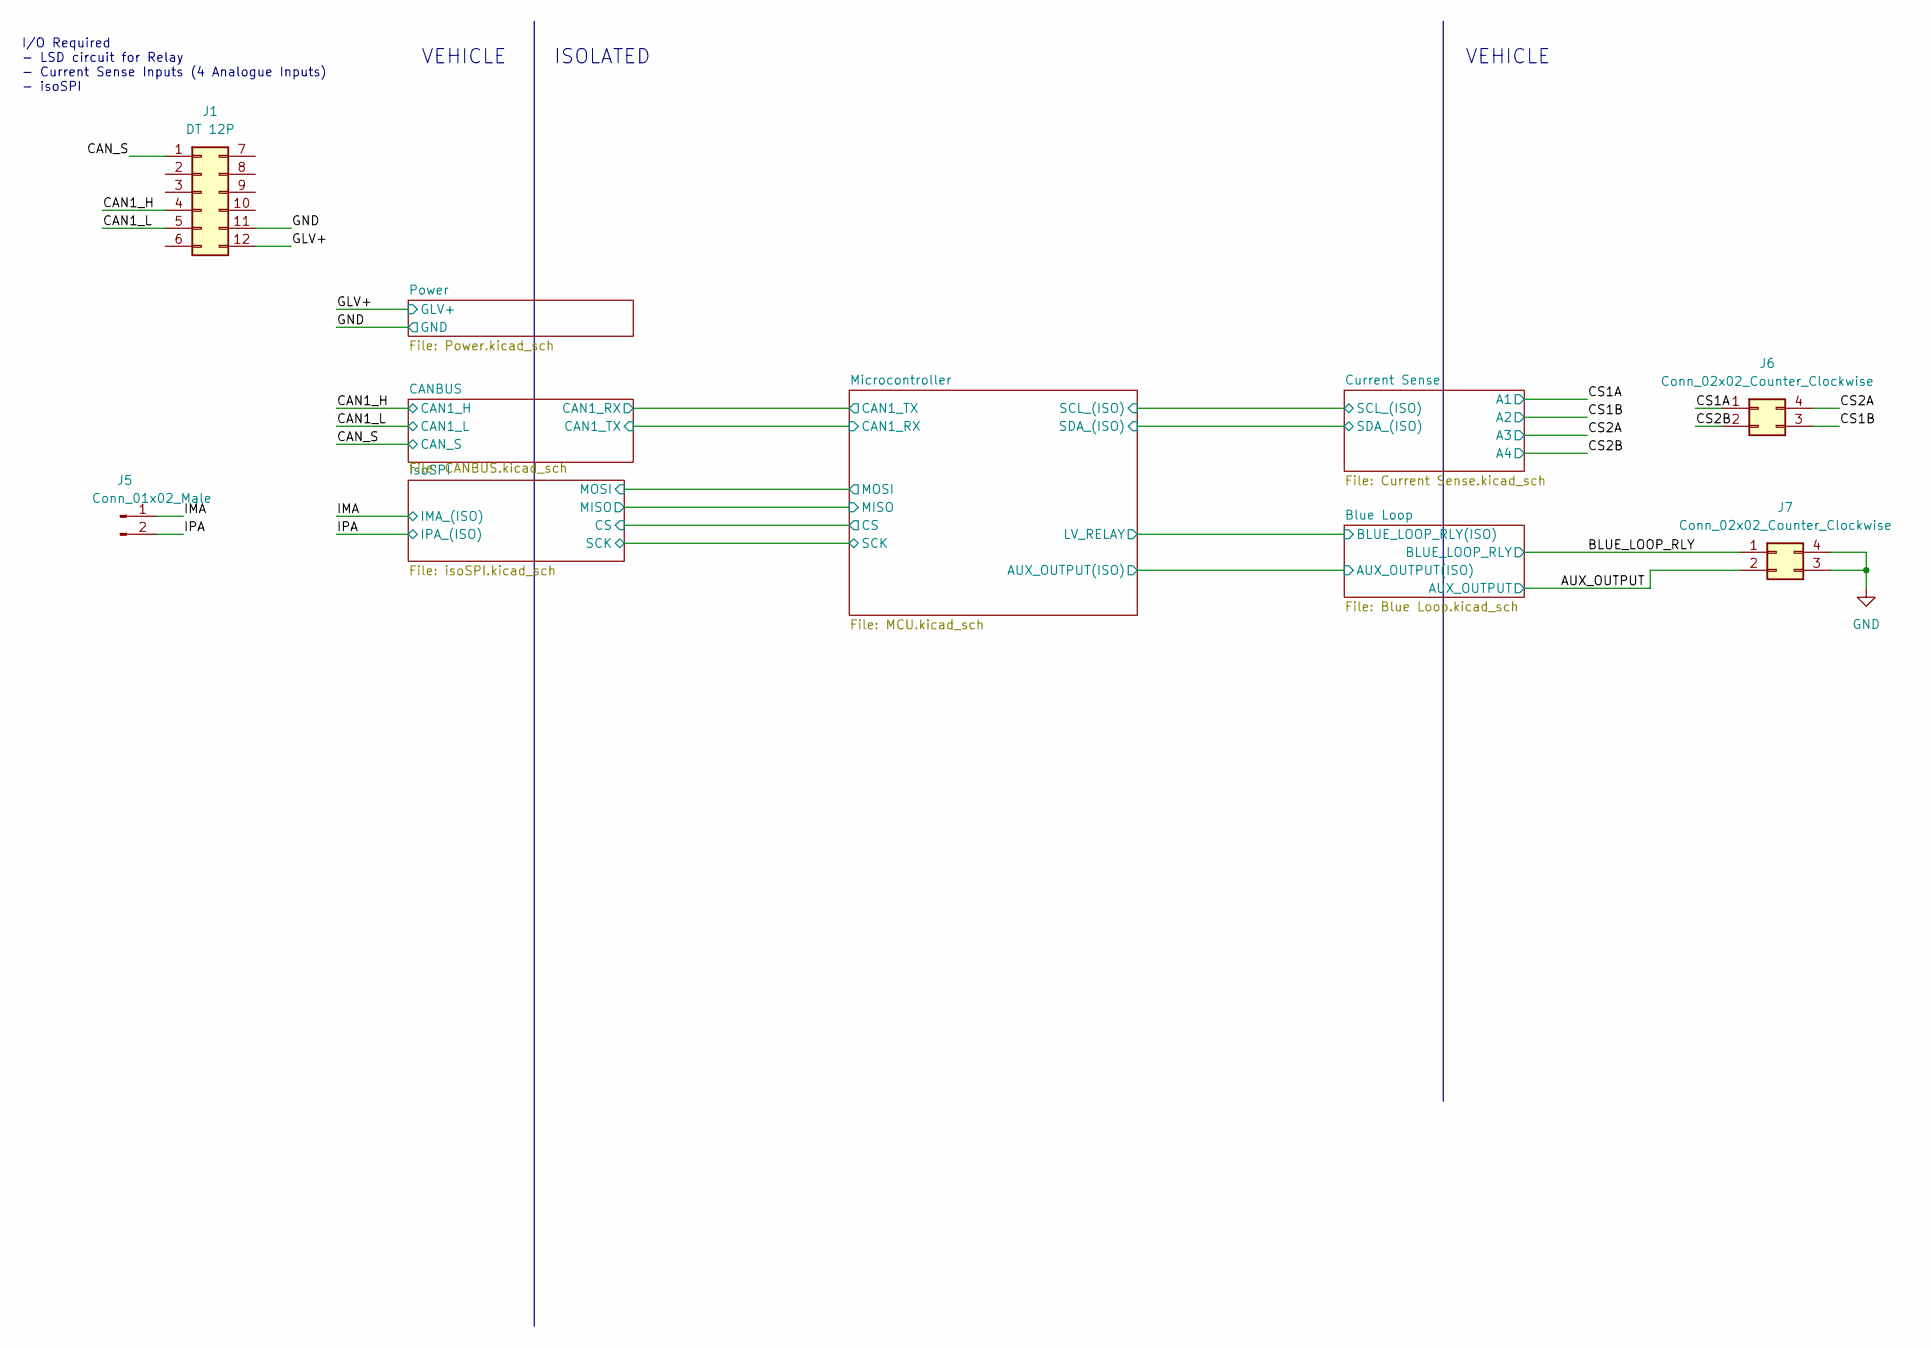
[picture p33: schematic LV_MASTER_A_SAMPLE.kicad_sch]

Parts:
J1: DT 12P; DT12-PCB PIN
J5: Conn_01x02_Male; Molex_Mini-Fit_Jr_5566-02A_2x01_P4.20mm_Vertical
J6, J7: Conn_02x02_Counter_Clockwise; Molex_Mini-Fit_Jr_5566-04A_2x02_P4.20mm_Vertical

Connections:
/AUX_OUTPUT: J7.2; also elsewhere on the board
/BLUE_LOOP_RLY: J7.1; also elsewhere on the board
/CAN1_H: J1.4; also elsewhere on the board
/CAN1_L: J1.5; also elsewhere on the board
/CS1A: J6.1; also elsewhere on the board
/CS1B: J6.3; also elsewhere on the board
/CS2A: J6.4; also elsewhere on the board
/CS2B: J6.2; also elsewhere on the board
/GLV+: J1.12; also elsewhere on the board
/IMA: J5.1; also elsewhere on the board
/IPA: J5.2; also elsewhere on the board

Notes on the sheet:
I/O Required - LSD circuit for Relay - Current Sense Inputs (4 Analogue Inputs) - isoSPI
VEHICLE
ISOLATED

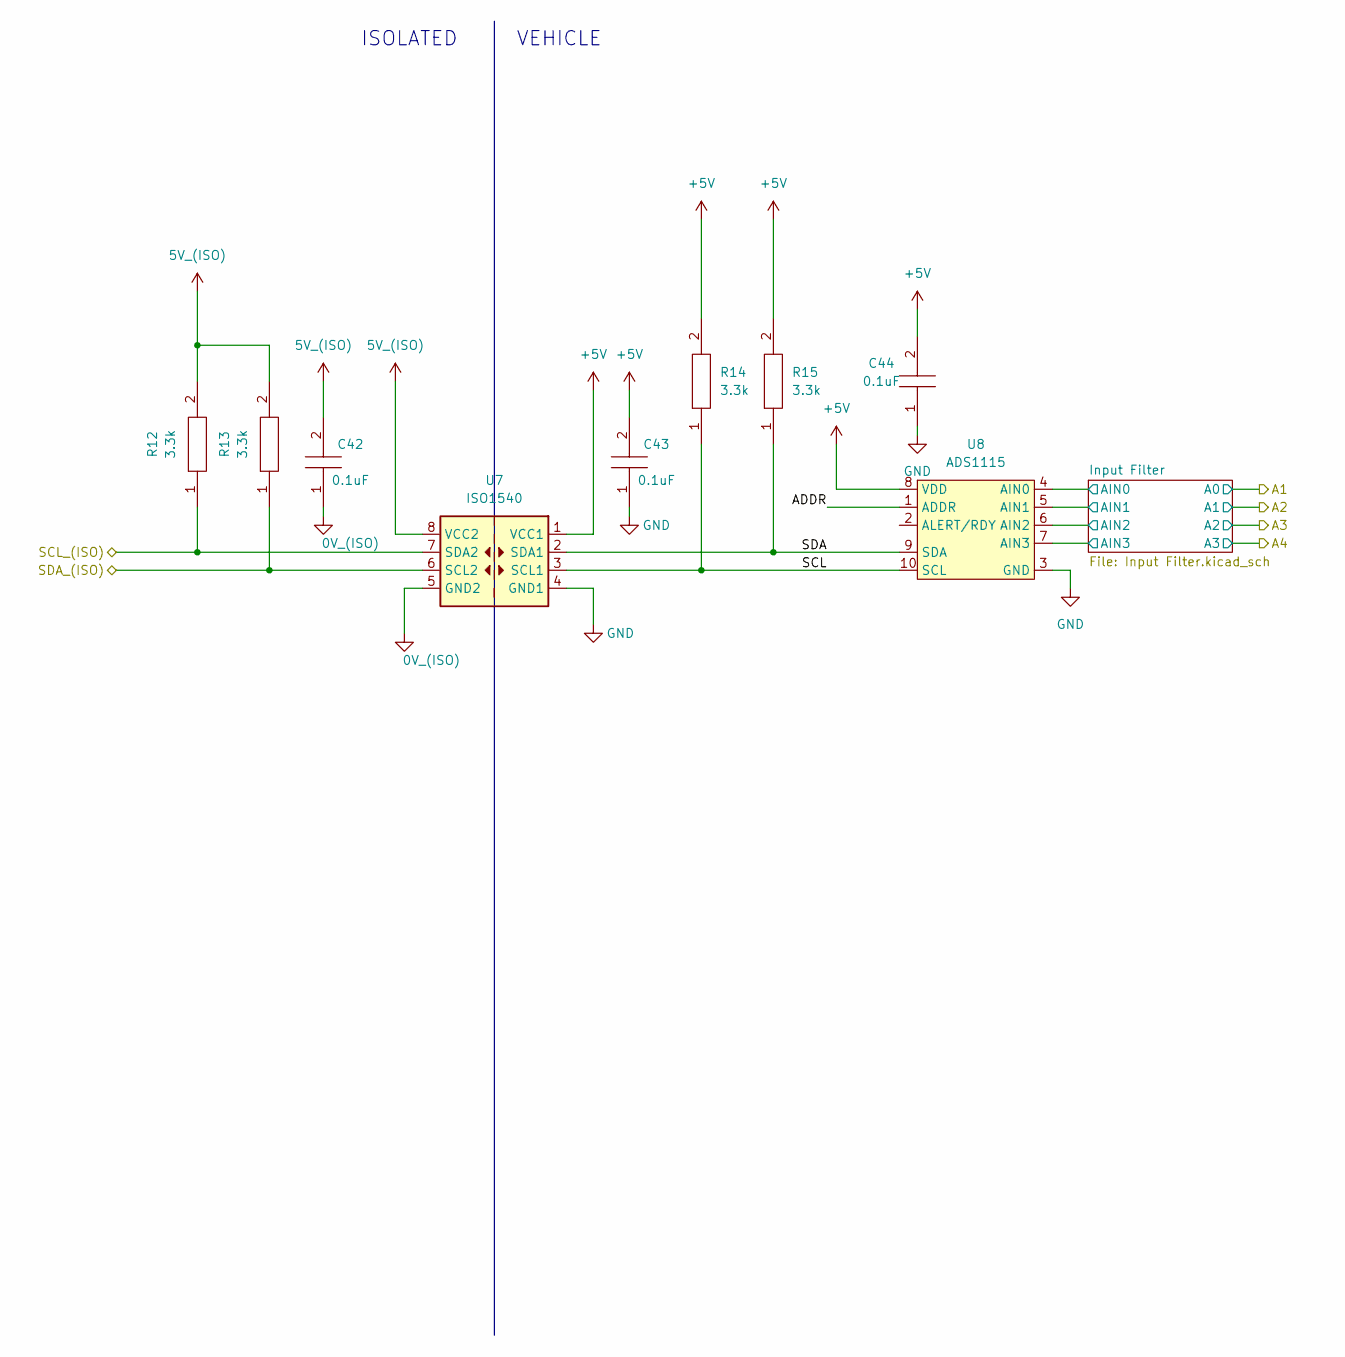
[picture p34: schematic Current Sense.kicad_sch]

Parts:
C42, C43, C44: 0.1uF; C_0603_1608Metric_Pad1.08x0.95mm_HandSolder; Manufacturer_Part_Number CC0805JRX7R8BB104; Mouser Part Number 603-CC805JRX7R8BB104
R12, R13, R14, R15: 3.3k; R_0603_1608Metric_Pad0.98x0.95mm_HandSolder; Manufacturer_Part_Number ERJP06F1000V
U7: ISO1540; SOIC-8_3.9x4.9mm_P1.27mm
U8: ADS1115; VSSOP-10_3x3mm_P0.5mm

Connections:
5V_(ISO): C42.2, R12.2, R13.2, U7.8 (VCC2); also elsewhere on the board
+5V: C43.2, C44.2, R14.2, R15.2, U7.1 (VCC1), U8.8 (VDD); also elsewhere on the board
/Current Sense/ADDR: U8.1 (ADDR)
/Current Sense/Input Filter/AIN0: U8.4 (AIN0); also elsewhere on the board
/Current Sense/Input Filter/AIN1: U8.5 (AIN1); also elsewhere on the board
/Current Sense/Input Filter/AIN2: U8.6 (AIN2); also elsewhere on the board
/Current Sense/Input Filter/AIN3: U8.7 (AIN3); also elsewhere on the board
/Current Sense/SCL: R14.1, U7.3 (SCL1), U8.10 (SCL)
/Current Sense/SDA: R15.1, U7.2 (SDA1), U8.9 (SDA)
/Microcontroller/SCL_(ISO): R12.1, U7.7 (SDA2); also elsewhere on the board
/Microcontroller/SDA_(ISO): R13.1, U7.6 (SCL2); also elsewhere on the board

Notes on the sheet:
ISOLATED
VEHICLE

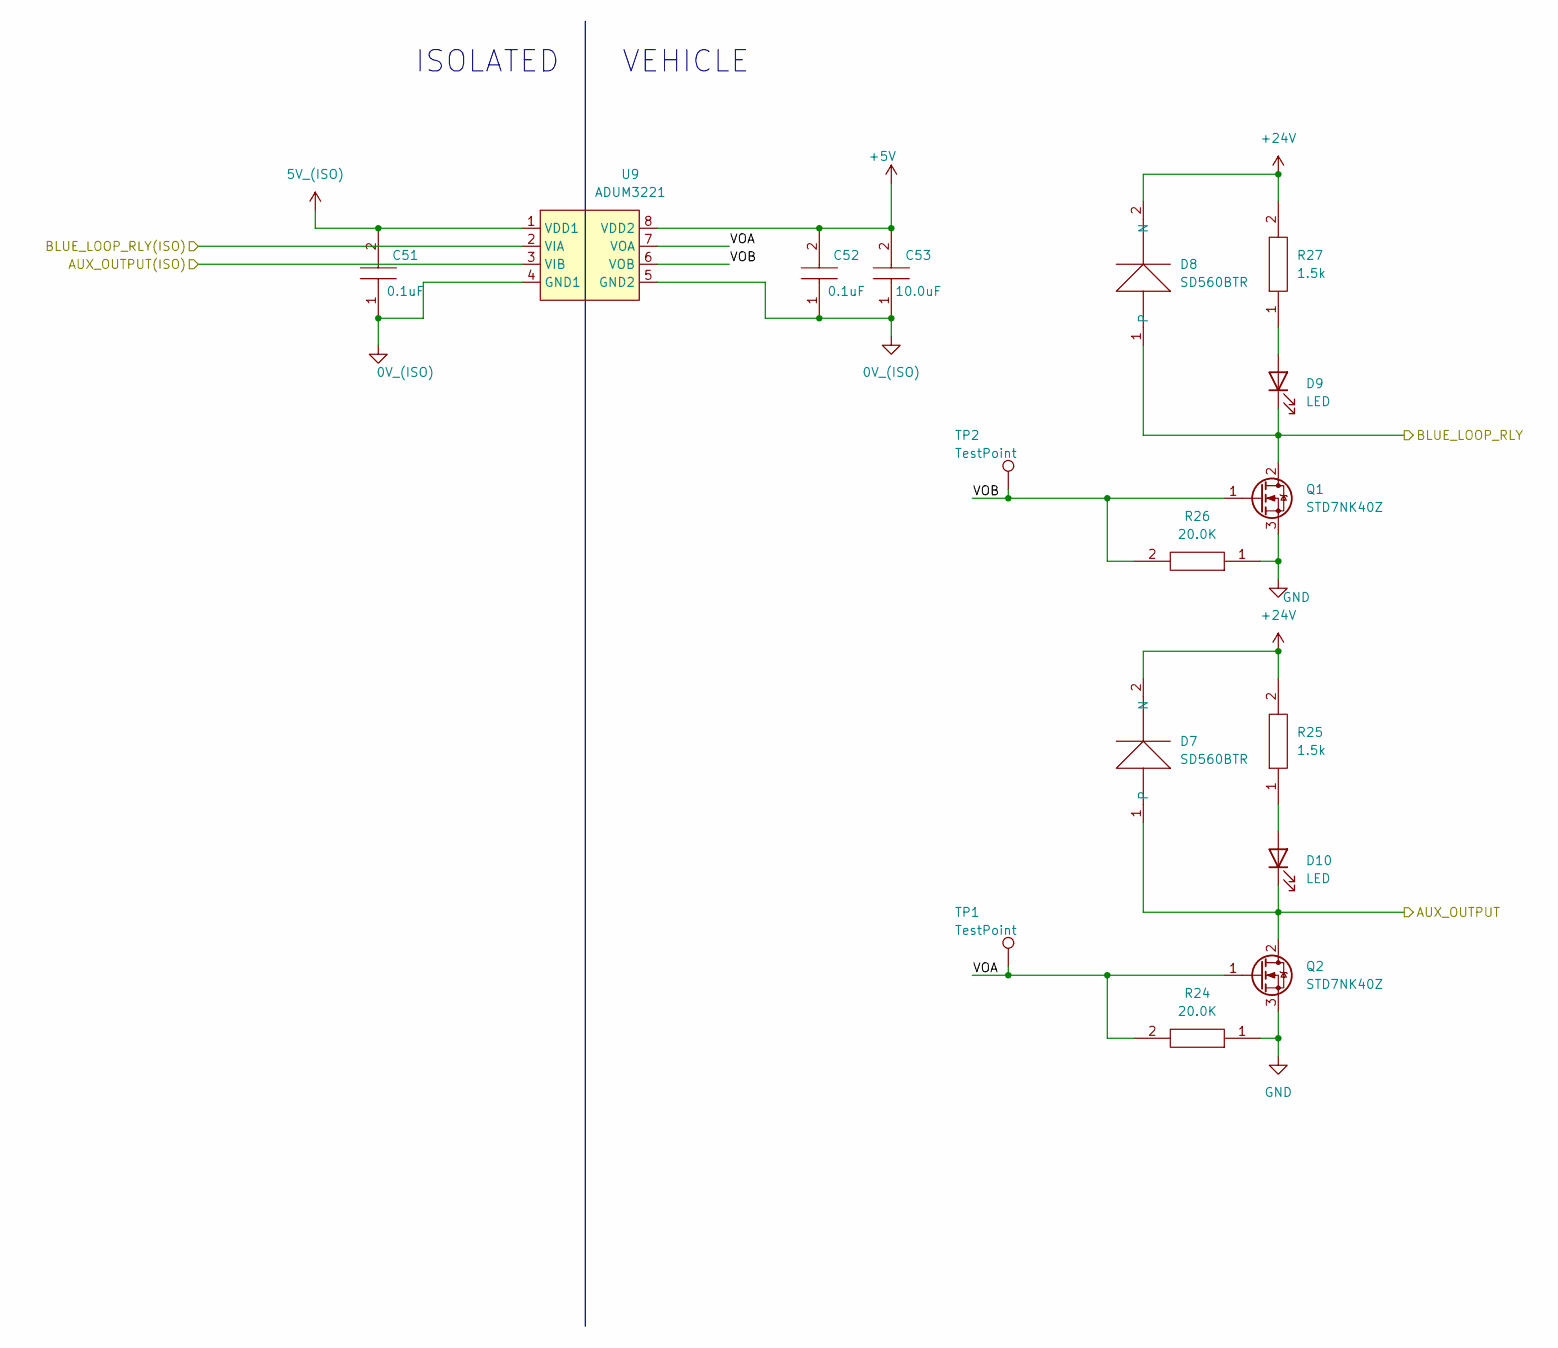
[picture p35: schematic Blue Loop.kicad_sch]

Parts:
C51, C52: 0.1uF; C_0603_1608Metric_Pad1.08x0.95mm_HandSolder; Manufacturer_Part_Number CC0805JRX7R8BB104; Mouser Part Number 603-CC805JRX7R8BB104
C53: 10.0uF; C_0603_1608Metric_Pad1.08x0.95mm_HandSolder; Manufacturer_Part_Number CC0805JRX7R8BB104; Mouser Part Number 603-CC805JRX7R8BB104
D7, D8: SD560BTR; D_SMB_Handsoldering
D9, D10: LED; LED_0805_2012Metric_Pad1.15x1.40mm_HandSolder
Q1, Q2: STD7NK40Z; TO-252-2
R24, R26: 20.0K; R_0603_1608Metric_Pad0.98x0.95mm_HandSolder; Manufacturer_Part_Number ERJP06F1000V
R25, R27: 1.5k; R_0603_1608Metric_Pad0.98x0.95mm_HandSolder; Manufacturer_Part_Number ERJP06F1000V
TP1, TP2: TestPoint; TestPoint_Pad_1.0x1.0mm
U9: ADUM3221; SOIC-8_3.9x4.9mm_P1.27mm

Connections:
5V_(ISO): C51.2, U9.1 (VDD1); also elsewhere on the board
+5V: C52.2, C53.2, U9.8 (VDD2); also elsewhere on the board
+24V: D7.2 (N), D8.2 (N), R25.2, R27.2; also elsewhere on the board
/AUX_OUTPUT: D7.1, D10.1 (K), Q2.2 (D); also elsewhere on the board
/BLUE_LOOP_RLY: D8.1, D9.1 (K), Q1.2 (D); also elsewhere on the board
/Blue Loop/AUX_OUTPUT(ISO): U9.3 (VIB); also elsewhere on the board
/Blue Loop/BLUE_LOOP_RLY(ISO): U9.2 (VIA); also elsewhere on the board
/Blue Loop/VOA: Q2.1 (G), R24.2, TP1.1, U9.7 (VOA); also elsewhere on the board
/Blue Loop/VOB: Q1.1 (G), R26.2, TP2.1, U9.6 (VOB); also elsewhere on the board
unnamed: D9.2 (A), R27.1
unnamed: D10.2 (A), R25.1

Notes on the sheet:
ISOLATED
VEHICLE

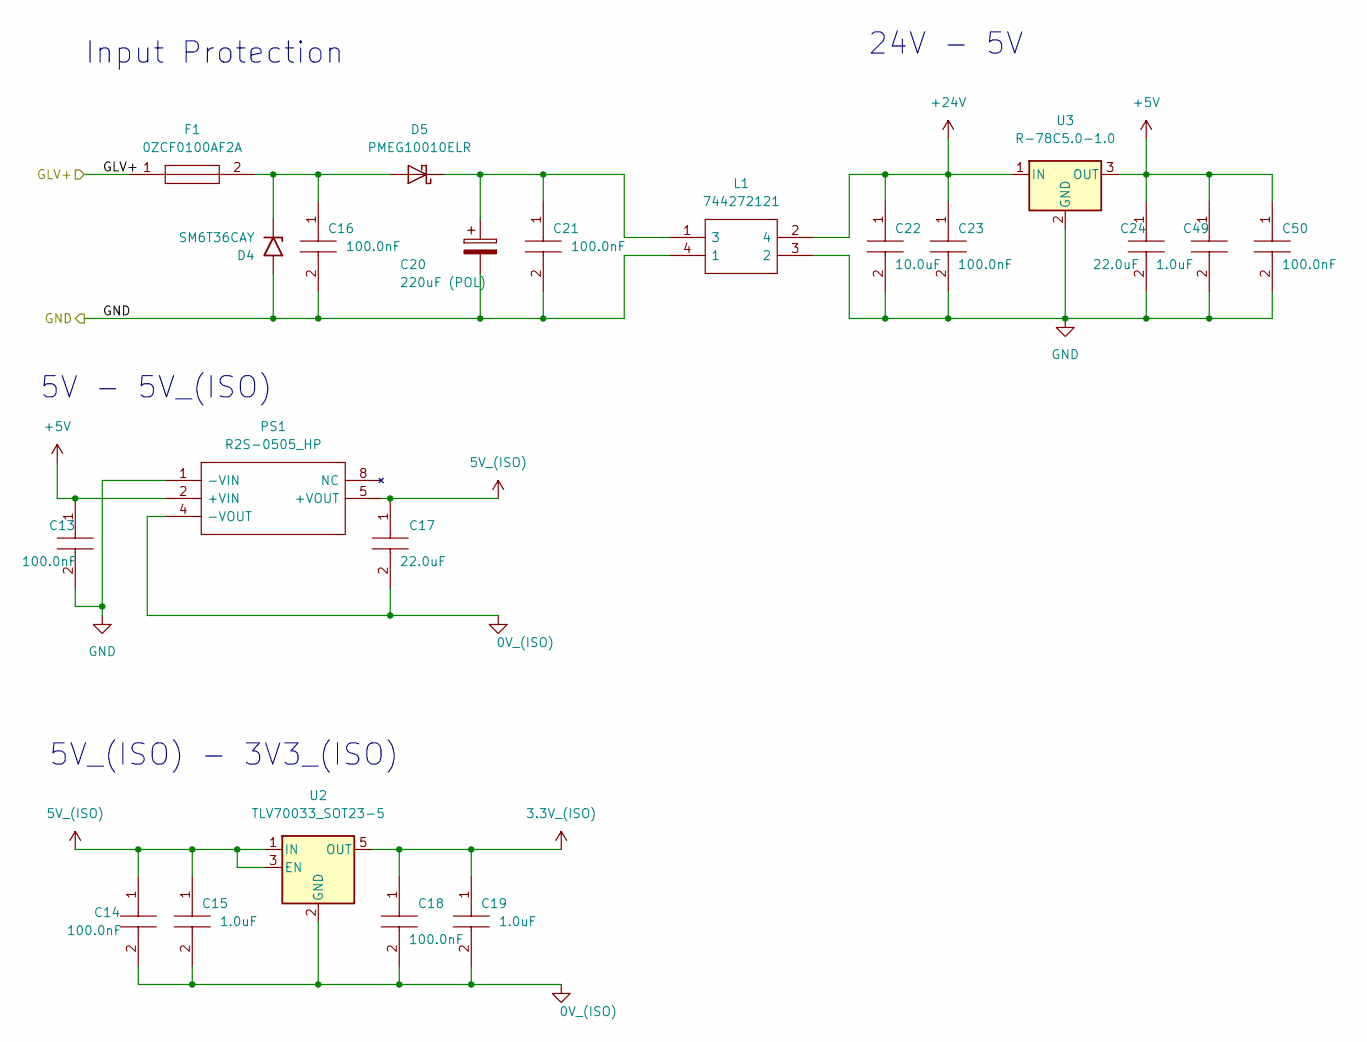
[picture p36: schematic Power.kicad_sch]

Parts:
C13, C14, C18, C21, C23, C50: 100.0nF; C_0603_1608Metric_Pad1.08x0.95mm_HandSolder; Manufacturer_Part_Number CC0805JRX7R8BB104; Mouser Part Number 603-CC805JRX7R8BB104
C15, C19, C49: 1.0uF; C_0603_1608Metric_Pad1.08x0.95mm_HandSolder; Manufacturer_Part_Number CC0805JRX7R8BB104; Mouser Part Number 603-CC805JRX7R8BB104
C16: 100.0nF; C_0805_2012Metric_Pad1.18x1.45mm_HandSolder; Manufacturer_Part_Number CC0805JRX7R8BB104; Mouser Part Number 603-CC805JRX7R8BB104
C17, C24: 22.0uF; C_0805_2012Metric_Pad1.18x1.45mm_HandSolder; Manufacturer_Part_Number CC0805JRX7R8BB104; Mouser Part Number 603-CC805JRX7R8BB104
C20: 220uF (POL); C_0805_2012Metric_Pad1.18x1.45mm_HandSolder
C22: 10.0uF; C_0603_1608Metric_Pad1.08x0.95mm_HandSolder; Manufacturer_Part_Number CC0805JRX7R8BB104; Mouser Part Number 603-CC805JRX7R8BB104
D4: SM6T36CAY; D_SMB
D5: PMEG10010ELR; Nexperia_CFP3_SOD-123W
F1: 0ZCF0100AF2A; FUSC7451X170N; Manufacturer_Part_Number 0ZCF0100AF2A; Mouser Part Number 530-0ZCF0100AF2A
L1: 744272121; WE-SL575; Manufacturer_Part_Number 744272121; Mouser Part Number 710-744272121
PS1: R2S-0505_HP; R2S0505HP; Manufacturer_Part_Number R2S-0505/HP; Mouser Part Number 919-R2S-0505HP
U2: TLV70033_SOT23-5; SOT-23-5
U3: R-78C5.0-1.0; Converter_DCDC_RECOM_R-78E-0.5_THT

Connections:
3.3V_(ISO): C18.1, C19.1, U2.5 (OUT); also elsewhere on the board
5V_(ISO): C14.1, C15.1, C17.1, PS1.5 (+VOUT), U2.1 (IN), U2.3 (EN); also elsewhere on the board
+5V: C13.1, C24.1, C49.1, C50.1, PS1.2 (+VIN), U3.3 (OUT); also elsewhere on the board
+24V: C22.1, C23.1, L1.2 (4), U3.1 (IN); also elsewhere on the board
/GLV+: F1.1; also elsewhere on the board
unnamed: C16.1, D4.1 (A1), D5.2 (A), F1.2
unnamed: C20.1, C21.1, D5.1 (K), L1.1 (3)

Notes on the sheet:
5V_(ISO) - 3V3_(ISO)
Input Protection
5V - 5V_(ISO)
24V - 5V

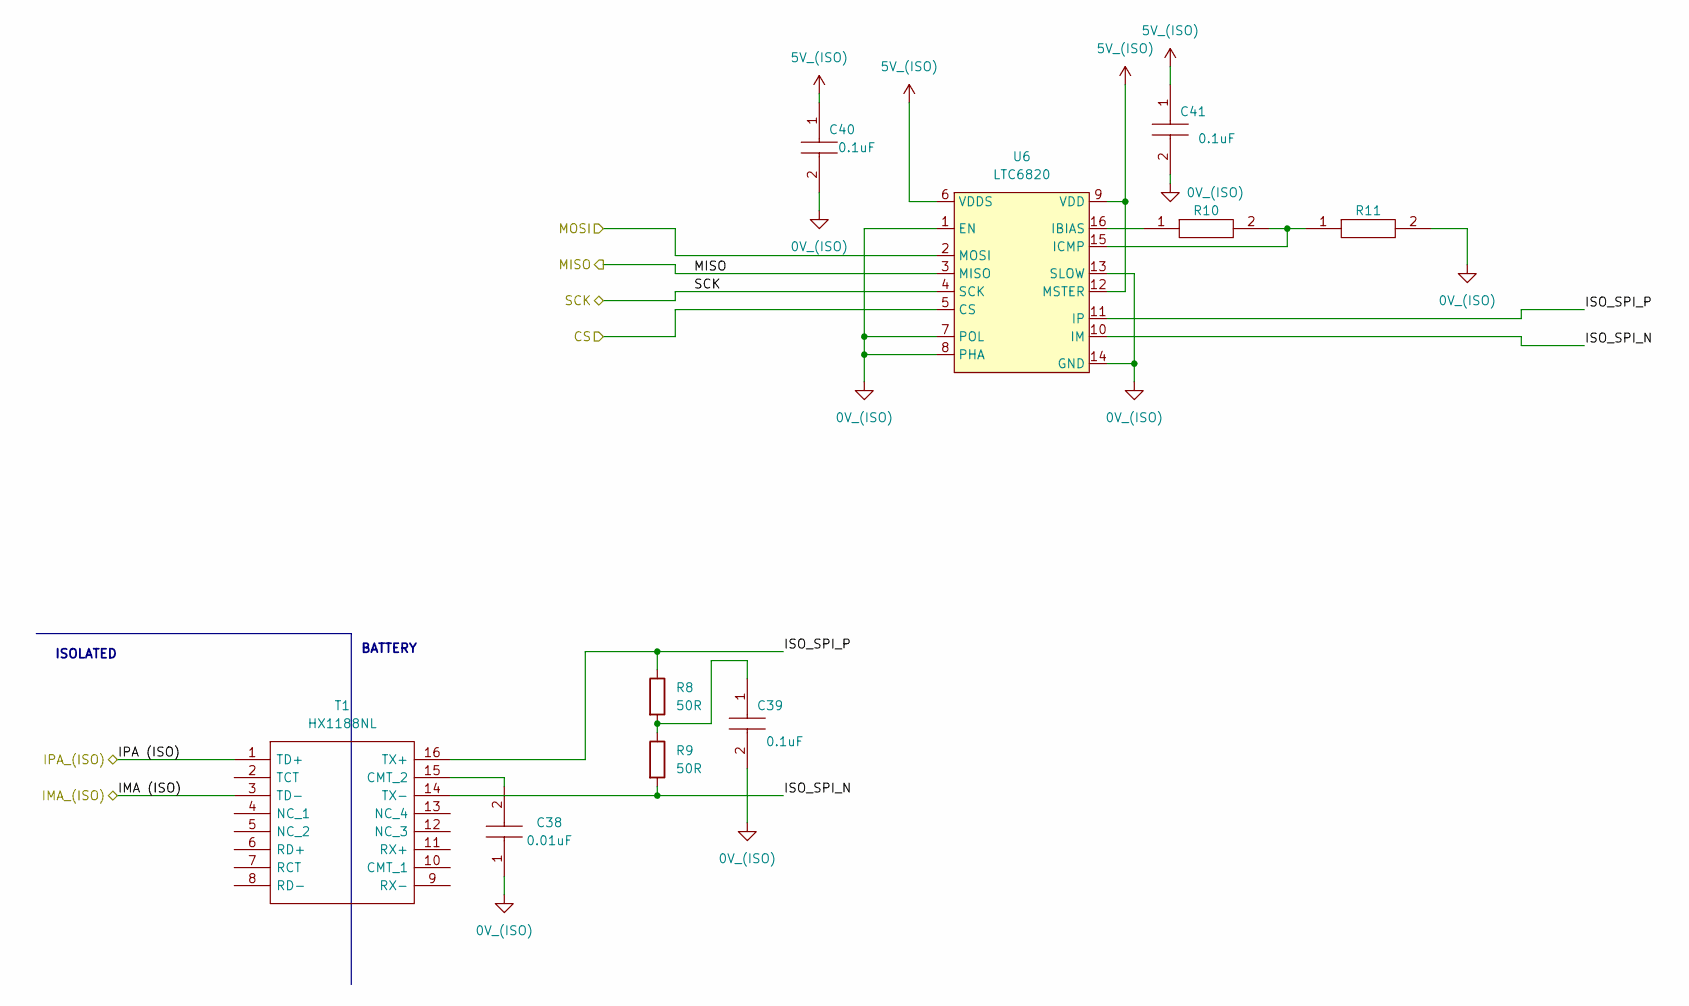
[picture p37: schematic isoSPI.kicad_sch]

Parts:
C38: 0.01uF; C_0603_1608Metric_Pad1.08x0.95mm_HandSolder; Manufacturer_Part_Number CC0805JRX7R9BB103
C39, C40, C41: 0.1uF; C_0603_1608Metric_Pad1.08x0.95mm_HandSolder; Manufacturer_Part_Number CC0805JRX7R8BB104; Mouser Part Number 603-CC805JRX7R8BB104
R8, R9: 50R; R_0603_1608Metric_Pad0.98x0.95mm_HandSolder
R10, R11: ERJP06F1000V; R_0603_1608Metric_Pad0.98x0.95mm_HandSolder; Manufacturer_Part_Number ERJP06F1000V
T1: HX1188NL; SOIC127P940X597-16N; Manufacturer_Part_Number HX1188NL; Mouser Part Number 673-HX1188NL
U6: LTC6820; MSOP-16_3x4.039mm_P0.5mm

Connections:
5V_(ISO): C40.1, C41.1, U6.6 (VDDS), U6.9 (VDD), U6.12 (MSTER); also elsewhere on the board
/IMA: T1.3 (TD-); also elsewhere on the board
/IPA: T1.1 (TD+); also elsewhere on the board
/Microcontroller/CS: U6.5 (CS); also elsewhere on the board
/Microcontroller/MISO: U6.3 (MISO); also elsewhere on the board
/Microcontroller/MOSI: U6.2 (MOSI); also elsewhere on the board
/Microcontroller/SCK: U6.4 (SCK); also elsewhere on the board
/isoSPI/ISO_SPI_N: R9.2, T1.14 (TX-), U6.10 (IM)
/isoSPI/ISO_SPI_P: R8.1, T1.16 (TX+), U6.11 (IP)
unnamed: C38.2, T1.15 (CMT_2)
unnamed: C39.1, R8.2, R9.1
unnamed: R10.1, U6.16 (IBIAS)
unnamed: R10.2, R11.1, U6.15 (ICMP)

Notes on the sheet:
ISOLATED
BATTERY

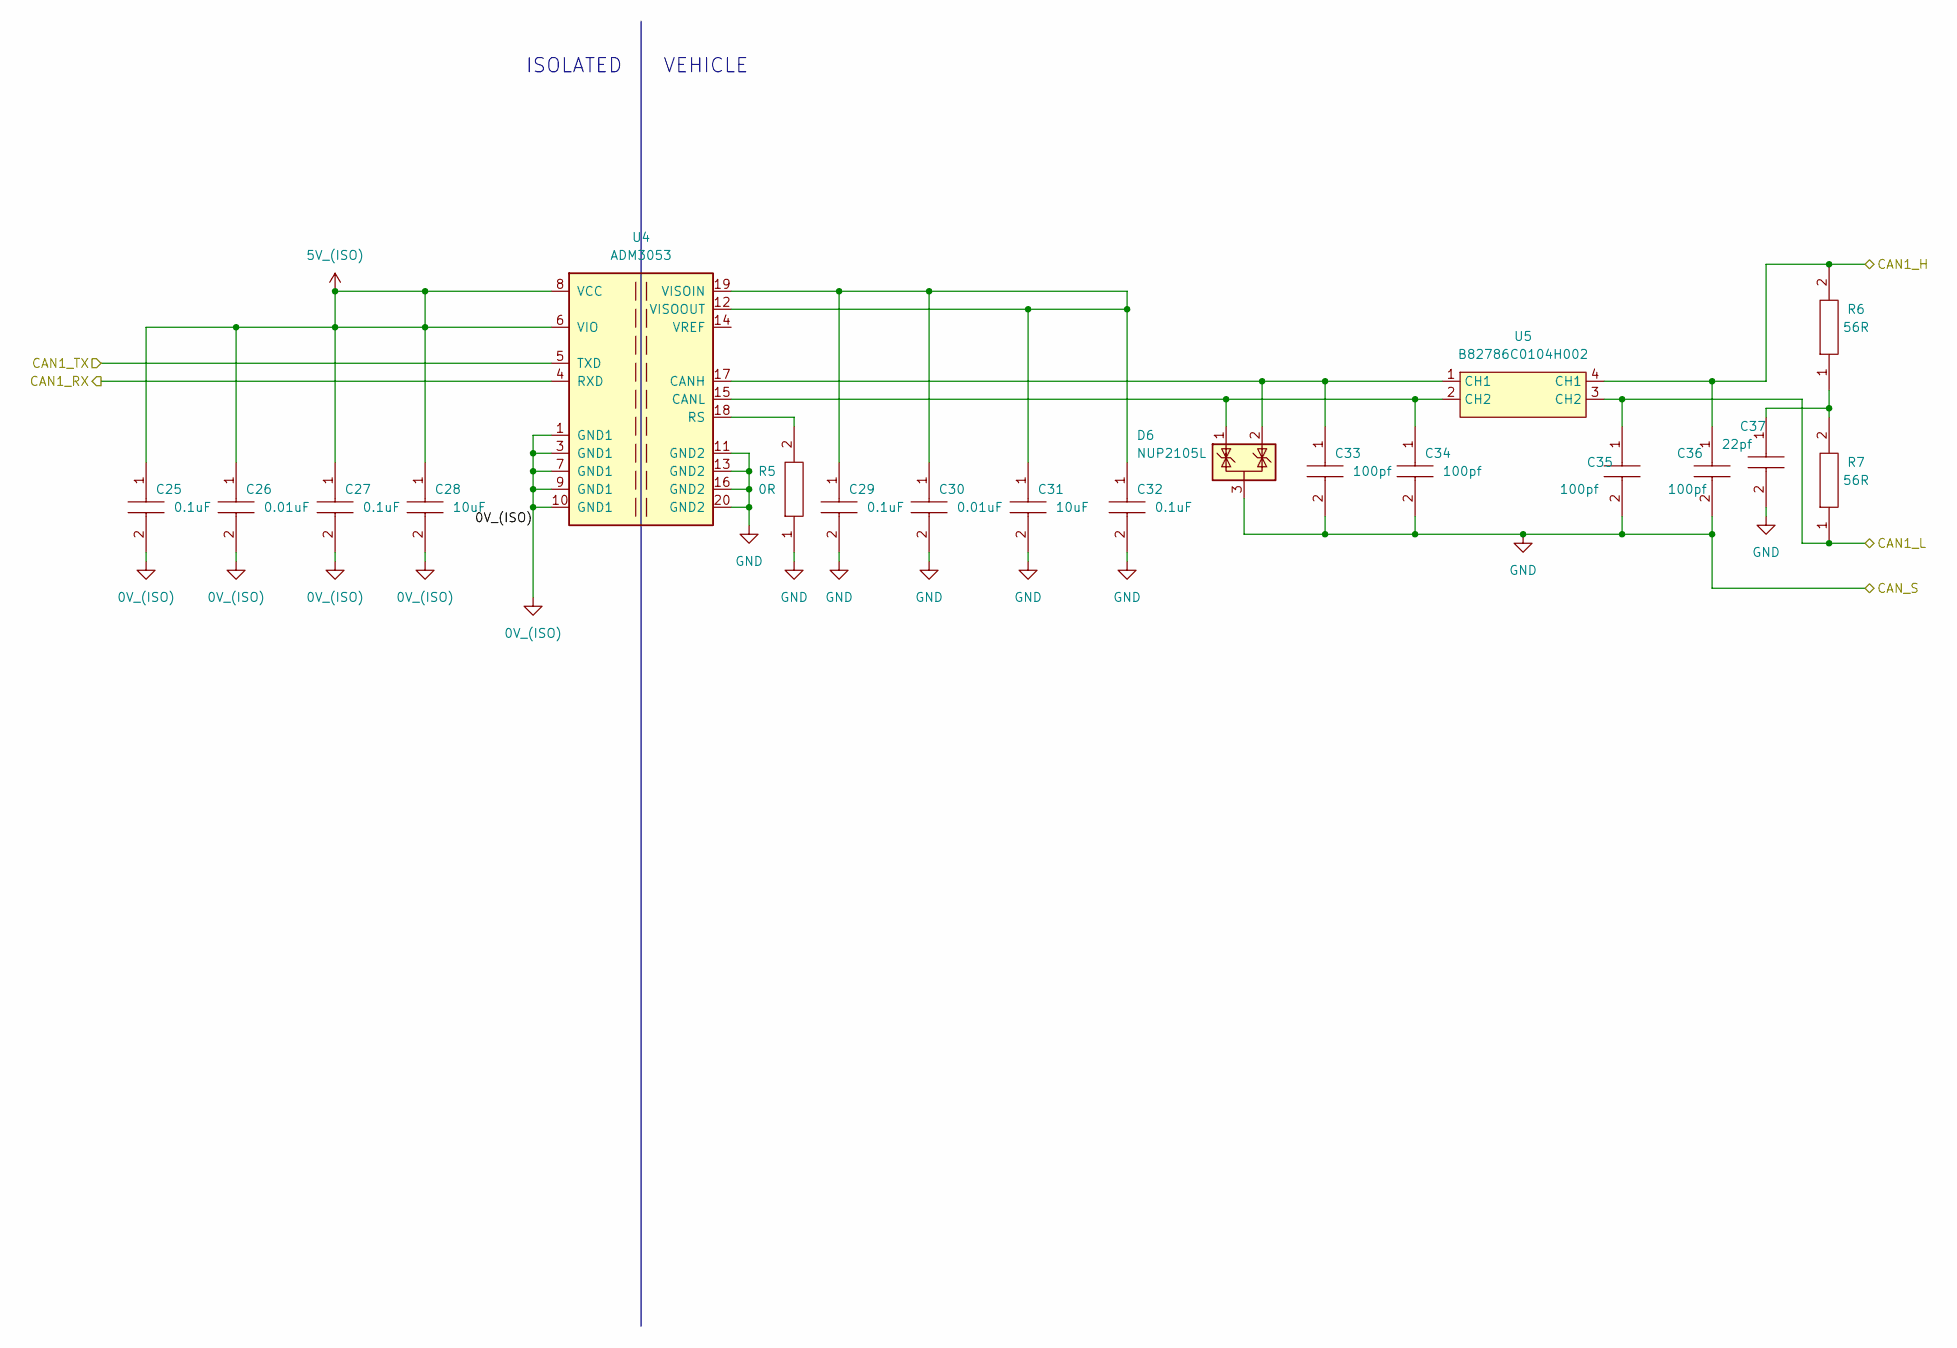
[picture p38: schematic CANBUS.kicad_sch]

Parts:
C25, C27, C29, C32: 0.1uF; C_0603_1608Metric_Pad1.08x0.95mm_HandSolder; Manufacturer_Part_Number CC0805JRX7R8BB104; Mouser Part Number 603-CC805JRX7R8BB104
C26, C30: 0.01uF; C_0603_1608Metric_Pad1.08x0.95mm_HandSolder; Manufacturer_Part_Number CC0805JRX7R8BB104; Mouser Part Number 603-CC805JRX7R8BB104
C28, C31: 10uF; C_0603_1608Metric_Pad1.08x0.95mm_HandSolder; Manufacturer_Part_Number CC0805JRX7R8BB104; Mouser Part Number 603-CC805JRX7R8BB104
C33, C34, C35, C36: 100pf; C_0603_1608Metric_Pad1.08x0.95mm_HandSolder; Manufacturer_Part_Number CC0805JRX7R8BB104; Mouser Part Number 603-CC805JRX7R8BB104
C37: 22pf; C_0603_1608Metric_Pad1.08x0.95mm_HandSolder; Manufacturer_Part_Number CC0805JRX7R8BB104; Mouser Part Number 603-CC805JRX7R8BB104
D6: NUP2105L; SOT-23
R5: 0R; R_0603_1608Metric_Pad0.98x0.95mm_HandSolder; Manufacturer_Part_Number ERJP06F1000V
R6, R7: 56R; R_0603_1608Metric_Pad0.98x0.95mm_HandSolder; Manufacturer_Part_Number ERJP06F1000V
U4: ADM3053; SOIC-20W_7.5x12.8mm_P1.27mm
U5: B82786C0104H002

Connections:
5V_(ISO): C25.1, C26.1, C27.1, C28.1, U4.6 (VIO), U4.8 (VCC); also elsewhere on the board
/CAN1_H: C36.1, R6.2, U5.4 (CH1); also elsewhere on the board
/CAN1_L: C35.1, R7.1, U5.3 (CH2); also elsewhere on the board
/CANBUS/CAN1_RX: U4.4 (RXD); also elsewhere on the board
/CANBUS/CAN1_TX: U4.5 (TXD); also elsewhere on the board
unnamed: C29.1, C30.1, C31.1, C32.1, U4.12 (VISOOUT), U4.19 (VISOIN)
unnamed: C33.1, D6.2 (K), U4.17 (CANH), U5.1 (CH1)
unnamed: C34.1, D6.1 (K), U4.15 (CANL), U5.2 (CH2)
unnamed: C37.1, R6.1, R7.2
unnamed: R5.2, U4.18 (RS)

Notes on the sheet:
VEHICLE
ISOLATED

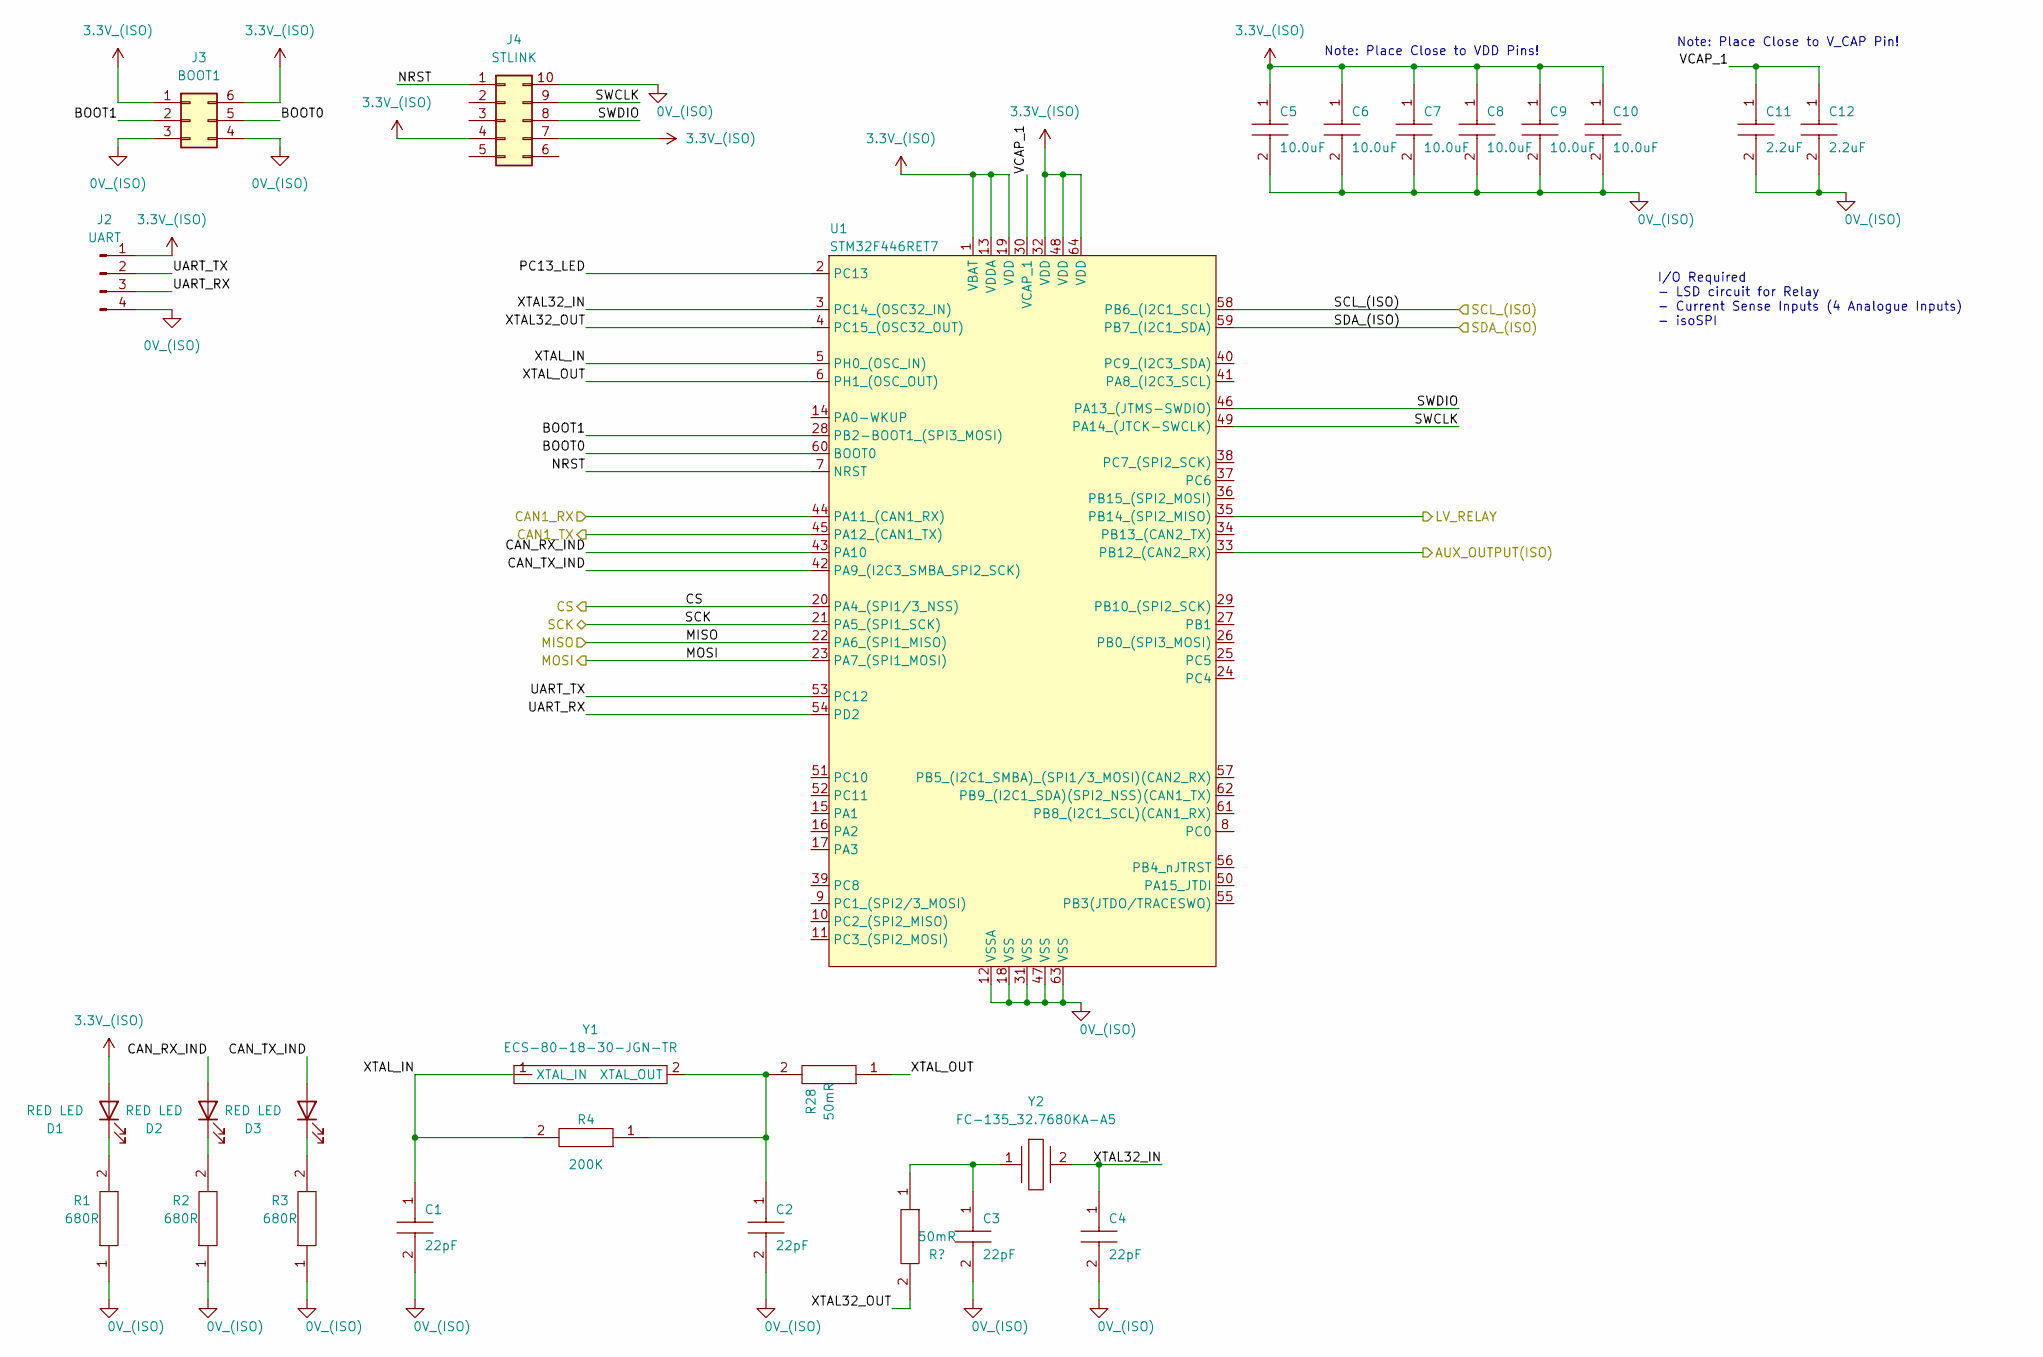
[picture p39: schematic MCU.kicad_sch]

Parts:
C1, C2, C3, C4: 22pF; C_0603_1608Metric_Pad1.08x0.95mm_HandSolder; Manufacturer_Part_Number CC0805JRX7R8BB104; Mouser Part Number 603-CC805JRX7R8BB104
C5, C6, C7, C8, C9, C10: 10.0uF; C_0603_1608Metric_Pad1.08x0.95mm_HandSolder; Manufacturer_Part_Number CC0805JRX7R8BB104; Mouser Part Number 603-CC805JRX7R8BB104
C11, C12: 2.2uF; C_0603_1608Metric_Pad1.08x0.95mm_HandSolder; Manufacturer_Part_Number CC0805JRX7R8BB104; Mouser Part Number 603-CC805JRX7R8BB104
D1, D2, D3: RED LED; C_0805_2012Metric_Pad1.18x1.45mm_HandSolder
J2: UART; PinHeader_1x04_P2.54mm_Vertical
J3: BOOT1; PinSocket_2x03_P2.54mm_Vertical
J4: STLINK; PinSocket_2x05_P2.54mm_Vertical_SMD
R1, R2, R3: 680R; R_0603_1608Metric_Pad0.98x0.95mm_HandSolder; Manufacturer_Part_Number ERJP06F1000V
R4: 200K; R_0603_1608Metric_Pad0.98x0.95mm_HandSolder; Manufacturer_Part_Number ERJP06F1000V
R28: 50mR; R_0603_1608Metric_Pad0.98x0.95mm_HandSolder; Manufacturer_Part_Number ERJP06F1000V
U1: STM32F446RET7; LQFP-64_10x10mm_P0.5mm
Y1: ECS-80-18-30-JGN-TR
Y2: FC-135_32.7680KA-A5; FC135327680KAA5; Manufacturer_Part_Number FC-135 32.7680KA-A5; Mouser Part Number 732-532.7680KA-A5

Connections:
3.3V_(ISO): C5.1, C6.1, C7.1, C8.1, C9.1, C10.1, D1.2 (A), J2.1, J3.1, J3.6, J4.4, J4.7, U1.1 (VBAT), U1.13 (VDDA), U1.19 (VDD), U1.32 (VDD), U1.48 (VDD), U1.64 (VDD); also elsewhere on the board
/Blue Loop/AUX_OUTPUT(ISO): U1.33 (PB12_(CAN2_RX)); also elsewhere on the board
/Blue Loop/BLUE_LOOP_RLY(ISO): U1.35 (PB14_(SPI2_MISO)); also elsewhere on the board
/CANBUS/CAN1_RX: U1.45 (PA12_(CAN1_TX)); also elsewhere on the board
/CANBUS/CAN1_TX: U1.44 (PA11_(CAN1_RX)); also elsewhere on the board
/Microcontroller/BOOT0: J3.5, U1.60 (BOOT0)
/Microcontroller/BOOT1: J3.2, U1.28 (PB2-BOOT1_(SPI3_MOSI))
/Microcontroller/CAN_RX_IND: D2.2 (A), U1.43 (PA10)
/Microcontroller/CAN_TX_IND: D3.2 (A), U1.42 (PA9_(I2C3_SMBA_SPI2_SCK))
/Microcontroller/CS: U1.20 (PA4_(SPI1/3_NSS)); also elsewhere on the board
/Microcontroller/MISO: U1.22 (PA6_(SPI1_MISO)); also elsewhere on the board
/Microcontroller/MOSI: U1.23 (PA7_(SPI1_MOSI)); also elsewhere on the board
/Microcontroller/NRST: J4.1, U1.7 (NRST)
/Microcontroller/PC13_LED: U1.2 (PC13)
/Microcontroller/SCK: U1.21 (PA5_(SPI1_SCK)); also elsewhere on the board
/Microcontroller/SCL_(ISO): U1.58 (PB6_(I2C1_SCL)); also elsewhere on the board
/Microcontroller/SDA_(ISO): U1.59 (PB7_(I2C1_SDA)); also elsewhere on the board
/Microcontroller/SWCLK: J4.9, U1.49 (PA14_(JTCK-SWCLK))
/Microcontroller/SWDIO: J4.8, U1.46 (PA13_(JTMS-SWDIO))
/Microcontroller/UART_RX: J2.3, U1.54 (PD2)
/Microcontroller/UART_TX: J2.2, U1.53 (PC12)
/Microcontroller/VCAP_1: C11.1, C12.1, U1.30 (VCAP_1)
/Microcontroller/XTAL32_IN: C4.1, U1.3 (PC14_(OSC32_IN)), Y2.2
/Microcontroller/XTAL32_OUT: U1.4 (PC15_(OSC32_OUT)); also elsewhere on the board
/Microcontroller/XTAL_IN: C1.1, R4.2, U1.5 (PH0_(OSC_IN)), Y1.1 (XTAL_IN)
/Microcontroller/XTAL_OUT: R28.1, U1.6 (PH1_(OSC_OUT))
unnamed: C2.1, R4.1, R28.2, Y1.2 (XTAL_OUT)
unnamed 52: C3.1, Y2.1; also elsewhere on the board
unnamed: D1.1 (K), R1.2
unnamed: D2.1 (K), R2.2
unnamed: D3.1 (K), R3.2

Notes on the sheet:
I/O Required - LSD circuit for Relay - Current Sense Inputs (4 Analogue Inputs) - isoSPI
Note: Place Close to VDD Pins!
Note: Place Close to V_CAP Pin!

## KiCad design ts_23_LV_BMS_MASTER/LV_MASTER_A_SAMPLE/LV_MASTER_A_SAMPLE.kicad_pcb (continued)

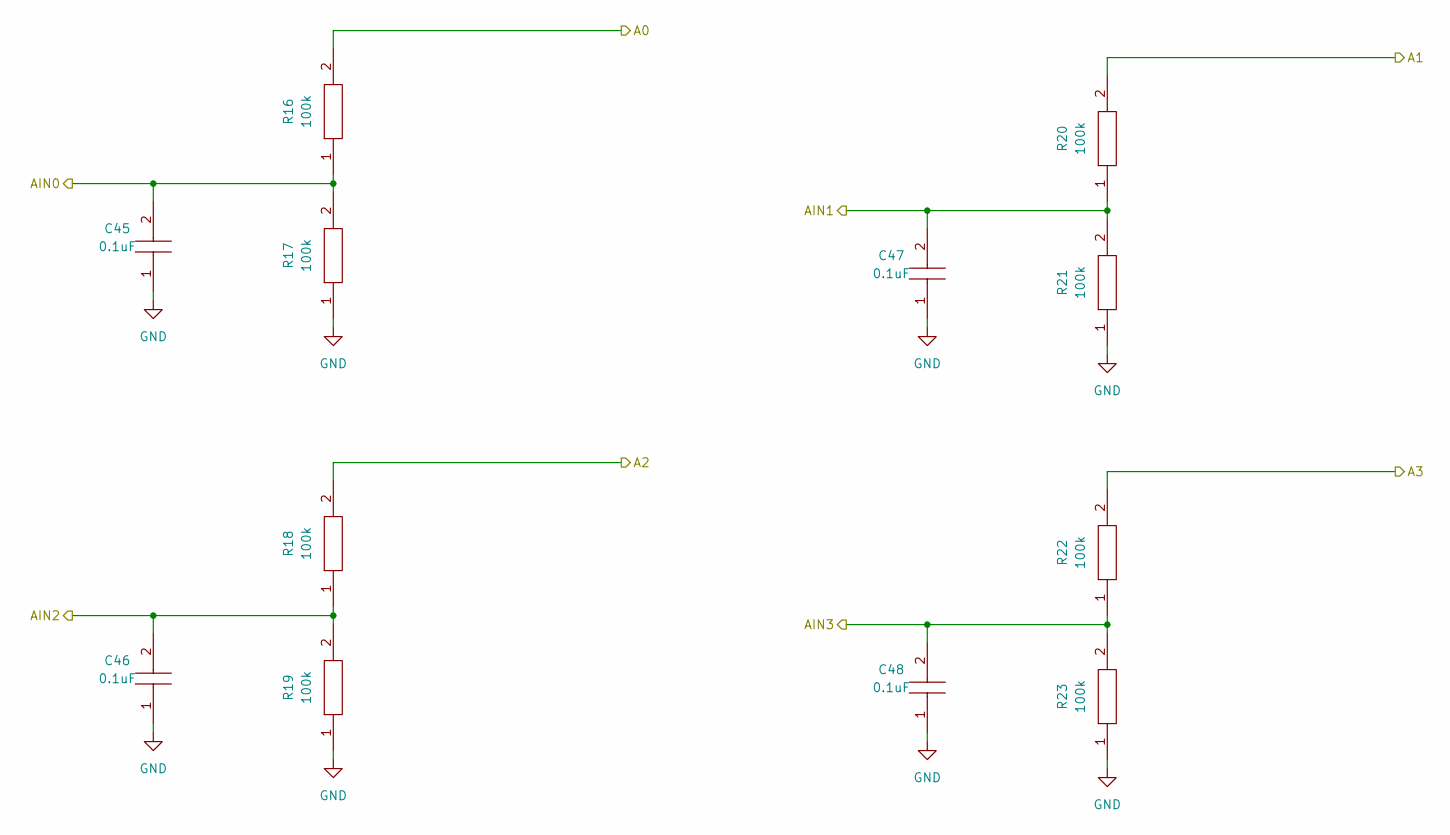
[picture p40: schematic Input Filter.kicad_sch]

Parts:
C45, C46, C47, C48: 0.1uF; C_0603_1608Metric_Pad1.08x0.95mm_HandSolder; Manufacturer_Part_Number CC0805JRX7R8BB104; Mouser Part Number 603-CC805JRX7R8BB104
R16, R17, R18, R19, R20, R21, R22, R23: 100k; R_0603_1608Metric_Pad0.98x0.95mm_HandSolder; Manufacturer_Part_Number ERJP06F1000V

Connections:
/CS1A: R16.2; also elsewhere on the board
/CS1B: R20.2; also elsewhere on the board
/CS2A: R18.2; also elsewhere on the board
/CS2B: R22.2; also elsewhere on the board
/Current Sense/Input Filter/AIN0: C45.2, R16.1, R17.2; also elsewhere on the board
/Current Sense/Input Filter/AIN1: C47.2, R20.1, R21.2; also elsewhere on the board
/Current Sense/Input Filter/AIN2: C46.2, R18.1, R19.2; also elsewhere on the board
/Current Sense/Input Filter/AIN3: C48.2, R22.1, R23.2; also elsewhere on the board

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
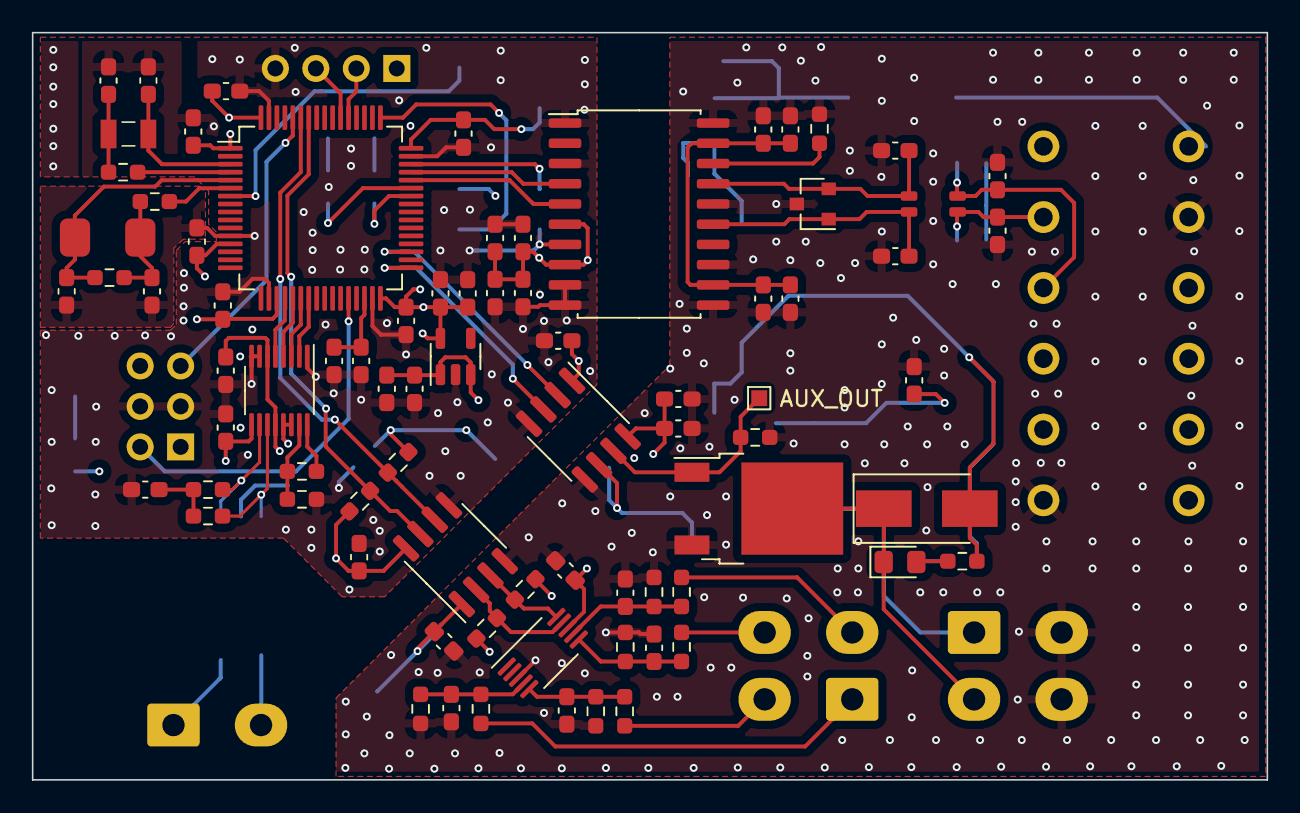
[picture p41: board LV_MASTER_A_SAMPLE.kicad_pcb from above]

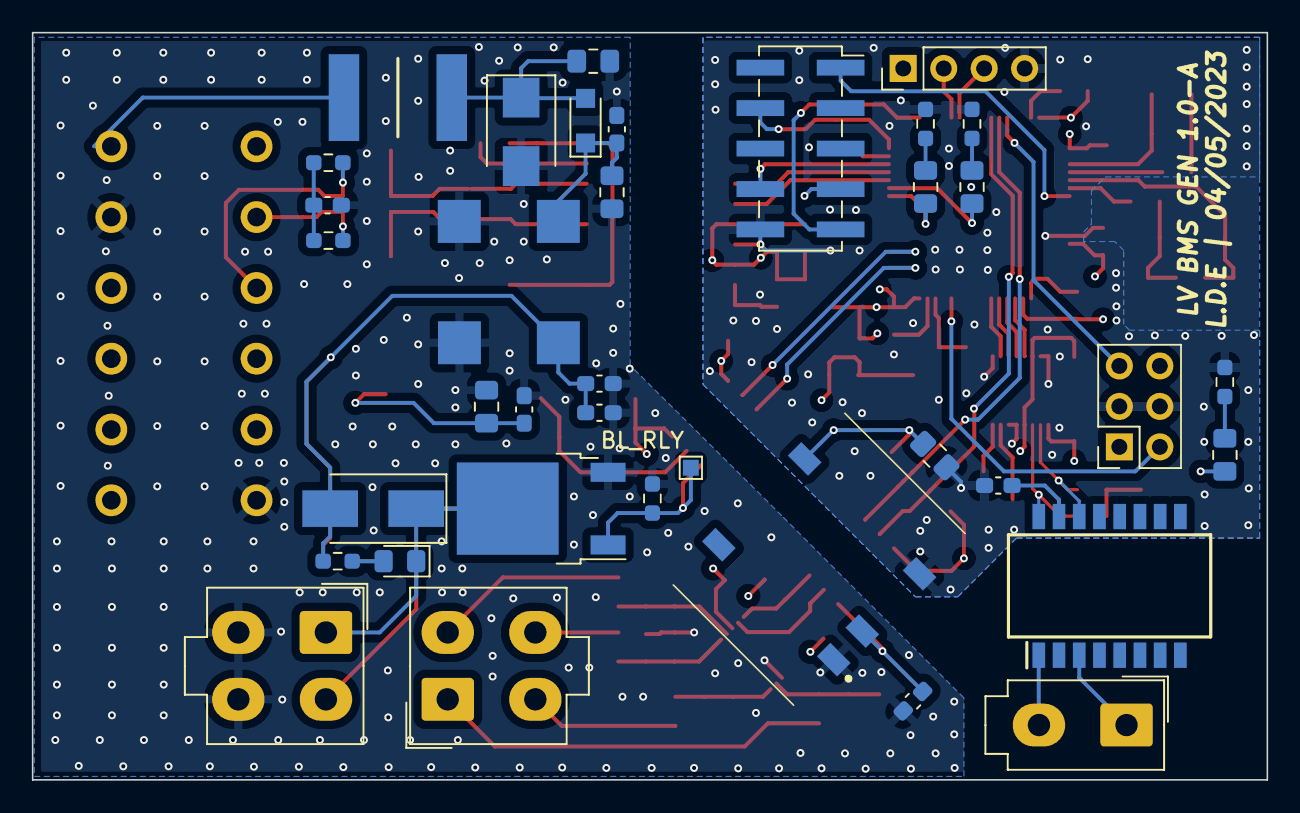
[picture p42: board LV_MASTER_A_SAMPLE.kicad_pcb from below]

Board: 4 copper layers, 77.5 x 46.9 mm, 117 parts (37 on the bottom side), 69 nets.

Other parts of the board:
AUX_OUT: AUX_OUT; TestPoint_Pad_1.0x1.0mm
BL_RLY: BL_RLY; TestPoint_Pad_1.0x1.0mm
R29: 50mR; R_0603_1608Metric_Pad0.98x0.95mm_HandSolder

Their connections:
/Blue Loop/VOA: AUX_OUT.1; also elsewhere on the board
/Blue Loop/VOB: BL_RLY.1; also elsewhere on the board
/Microcontroller/XTAL32_OUT: R29.2; also elsewhere on the board
unnamed 52: R29.1; also elsewhere on the board

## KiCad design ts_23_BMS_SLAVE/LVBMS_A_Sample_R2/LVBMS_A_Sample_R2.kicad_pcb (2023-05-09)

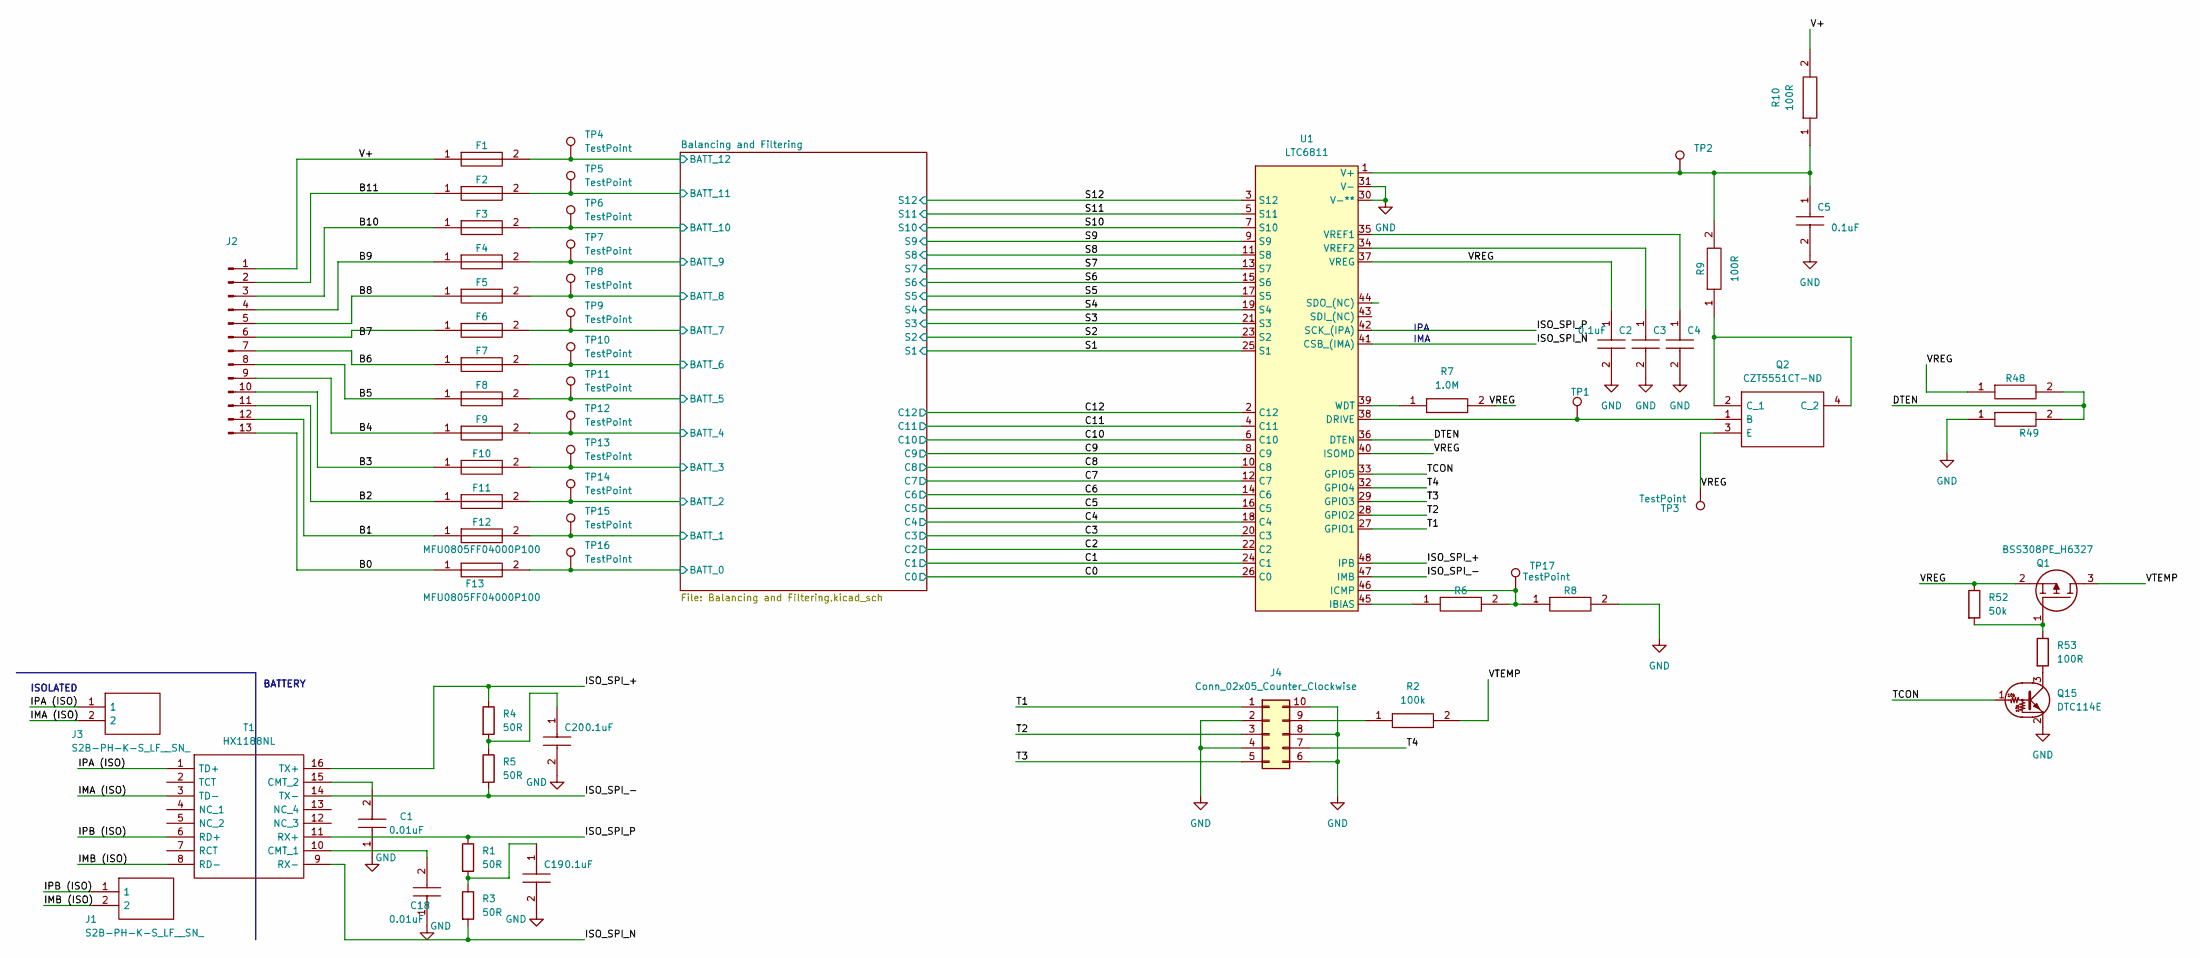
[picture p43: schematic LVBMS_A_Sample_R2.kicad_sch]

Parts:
C1, C18: 0.01uF; C_0603_1608Metric_Pad1.08x0.95mm_HandSolder; Manufacturer_Part_Number CC0805JRX7R9BB103
C2, C3, C4, C5, C19, C20: 0.1uF; C_0603_1608Metric_Pad1.08x0.95mm_HandSolder; Manufacturer_Part_Number CC0805JRX7R8BB104; Mouser Part Number 603-CC805JRX7R8BB104
F1, F2, F3, F4, F5, F6, F7, F8, F9, F10, F11, F12, F13: MFU0805FF04000P100; Fuse_0603_1608Metric_Pad1.05x0.95mm_HandSolder; Manufacturer_Part_Number MFU0805FF04000P100; Mouser Part Number 594-MFU0805FF04000P1
J1, J3: S2B-PH-K-S_LF__SN_; Molex_Mini-Fit_Jr_5566-02A_2x01_P4.20mm_Vertical; Manufacturer_Part_Number S2B-PH-K-S(LF)(SN)
J2: Conn_01x13_Male; PinSocket_1x13_P2.54mm_Vertical
J4: Conn_02x05_Counter_Clockwise; PinSocket_2x05_P2.54mm_Vertical
Q1: BSS308PE_H6327; SOT95P260X110-3N; Manufacturer_Part_Number BSS308PE H6327; Mouser Part Number 726-BSS308PEH6327
Q2: CZT5551CT-ND; SOT230P700X180-4N; Manufacturer_Part_Number CZT5551CT-ND
Q15: DTC114E; SOT-23
R1, R3, R4, R5: 50R; R_0603_1608Metric_Pad0.98x0.95mm_HandSolder
R2: 100k; R_0603_1608Metric_Pad0.98x0.95mm_HandSolder; Manufacturer_Part_Number ERJP06F1000V
R6: BIAS RESISTOR (VALUE CHANGES); R_0603_1608Metric_Pad0.98x0.95mm_HandSolder; Manufacturer_Part_Number ERJP06F1000V
R7: 1.0M; R_0603_1608Metric_Pad0.98x0.95mm_HandSolder; Manufacturer_Part_Number ERJ-P06J105V; Mouser Part Number 667-ERJ-P06J105V
R8: BIAS RESISTOR (VALUE CAN CHANGE); R_0603_1608Metric_Pad0.98x0.95mm_HandSolder; Manufacturer_Part_Number ERJP06F1000V
R9, R10, R48, R49: 100R; R_0603_1608Metric_Pad0.98x0.95mm_HandSolder; Manufacturer_Part_Number ERJP06F1000V
R52: 50k; R_0603_1608Metric_Pad0.98x0.95mm_HandSolder
R53: 100R; R_0603_1608Metric_Pad0.98x0.95mm_HandSolder
T1: HX1188NL; SOIC127P940X597-16N; Manufacturer_Part_Number HX1188NL; Mouser Part Number 673-HX1188NL
TP1, TP2, TP3, TP4, TP5, TP6, TP7, TP8, TP9, TP10, TP11, TP12, TP13, TP14, TP15, TP16, TP17: TestPoint; TestPoint_Pad_D1.0mm
U1: LTC6811

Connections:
/B0: F13.1, J2.13
/B1: F12.1, J2.12
/B2: F11.1, J2.11
/B3: F10.1, J2.10
/B4: F9.1, J2.9
/B5: F8.1, J2.8
/B6: F7.1, J2.7
/B8: F5.1, J2.5
/B9: F4.1, J2.4
/B10: F3.1, J2.3
/B11: F2.1, J2.2
/Balancing and Filtering/BATT_0: F13.2, TP16.1; also elsewhere on the board
/Balancing and Filtering/BATT_1: F12.2, TP15.1; also elsewhere on the board
/Balancing and Filtering/BATT_2: F11.2, TP14.1; also elsewhere on the board
/Balancing and Filtering/BATT_3: F10.2, TP13.1; also elsewhere on the board
/Balancing and Filtering/BATT_4: F9.2, TP12.1; also elsewhere on the board
/Balancing and Filtering/BATT_5: F8.2, TP11.1; also elsewhere on the board
/Balancing and Filtering/BATT_6: F7.2, TP10.1; also elsewhere on the board
/Balancing and Filtering/BATT_7: F6.2, TP9.1; also elsewhere on the board
/Balancing and Filtering/BATT_8: F5.2, TP8.1; also elsewhere on the board
/Balancing and Filtering/BATT_9: F4.2, TP7.1; also elsewhere on the board
/Balancing and Filtering/BATT_10: F3.2, TP6.1; also elsewhere on the board
/Balancing and Filtering/BATT_11: F2.2, TP5.1; also elsewhere on the board
/Balancing and Filtering/BATT_12: F1.2, TP4.1; also elsewhere on the board
/C1: U1.24 (C1); also elsewhere on the board
/C2: U1.22 (C2); also elsewhere on the board
/C3: U1.20 (C3); also elsewhere on the board
/C4: U1.18 (C4); also elsewhere on the board
/C5: U1.16 (C5); also elsewhere on the board
/C6: U1.14 (C6); also elsewhere on the board
/C7: U1.12 (C7); also elsewhere on the board
/C8: U1.10 (C8); also elsewhere on the board
/C9: U1.8 (C9); also elsewhere on the board
/C10: U1.6 (C10); also elsewhere on the board
/C11: U1.4 (C11); also elsewhere on the board
/C12: U1.2 (C12); also elsewhere on the board
/DTEN: R48.2, R49.2, U1.36 (DTEN)
/IMA (ISO): J3.2, T1.3 (TD-)
/IMB (ISO): J1.2, T1.8 (RD-)
/IPA (ISO): J3.1, T1.1 (TD+)
/IPB (ISO): J1.1, T1.6 (RD+)
/ISO_SPI_+: R4.1, T1.16 (TX+), U1.48 (IPB)
/ISO_SPI_-: R5.2, T1.14 (TX-), U1.47 (IMB)
/ISO_SPI_N: R3.2, T1.9 (RX-), U1.41 (CSB_(IMA))
/ISO_SPI_P: R1.1, T1.11 (RX+), U1.42 (SCK_(IPA))
/S1: U1.25 (S1); also elsewhere on the board
/S2: U1.23 (S2); also elsewhere on the board
/S3: U1.21 (S3); also elsewhere on the board
/S4: U1.19 (S4); also elsewhere on the board
/S5: U1.17 (S5); also elsewhere on the board
/S6: U1.15 (S6); also elsewhere on the board
/S7: U1.13 (S7); also elsewhere on the board
/S8: U1.11 (S8); also elsewhere on the board
/S9: U1.9 (S9); also elsewhere on the board
/S10: U1.7 (S10); also elsewhere on the board
/S11: U1.5 (S11); also elsewhere on the board
/S12: U1.3 (S12); also elsewhere on the board
/T1: J4.1, U1.27 (GPIO1)
/T2: J4.3, U1.28 (GPIO2)
/T3: J4.5, U1.29 (GPIO3)
/T4: J4.7, U1.32 (GPIO4)
/TCON: Q15.1 (B), U1.33 (GPIO5)
/V+: F1.1, J2.1, R10.2
/VREG: C2.1, Q1.2, Q2.3 (E), R7.2, R48.1, R52.1, TP3.1, U1.37 (VREG), U1.40 (ISOMD)
/VTEMP: Q1.3, R2.2
GND: C1.1, C2.2, C3.2, C4.2, C5.2, C18.1, C19.2, C20.2, J4.2, J4.4, J4.6, J4.8, J4.10, Q15.2 (E), R8.2, R49.1, U1.26 (C0), U1.30 (V-**), U1.31 (V-); also elsewhere on the board
unnamed: C1.2, T1.15 (CMT_2)
unnamed: C3.1, U1.34 (VREF2)
unnamed: C4.1, U1.35 (VREF1)
unnamed: C5.1, R9.2, R10.1, TP2.1, U1.1 (V+)
unnamed: C19.1, R1.2, R3.1
unnamed: C20.1, R4.2, R5.1
unnamed: F6.1, J2.6
unnamed: J4.9, R2.1
unnamed: Q1.1, R52.2, R53.1
unnamed: Q2.1 (B), TP1.1, U1.38 (DRIVE)
unnamed: Q2.2 (C_1), Q2.4 (C_2), R9.1
unnamed: Q15.3 (C), R53.2
unnamed: R7.1, U1.39 (WDT)
unnamed: C18.2, T1.10 (CMT_1)
unnamed: R6.1, U1.45 (IBIAS)
unnamed: R6.2, R8.1, TP17.1, U1.46 (ICMP)

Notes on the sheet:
IPA IMA
BATTERY
ISOLATED

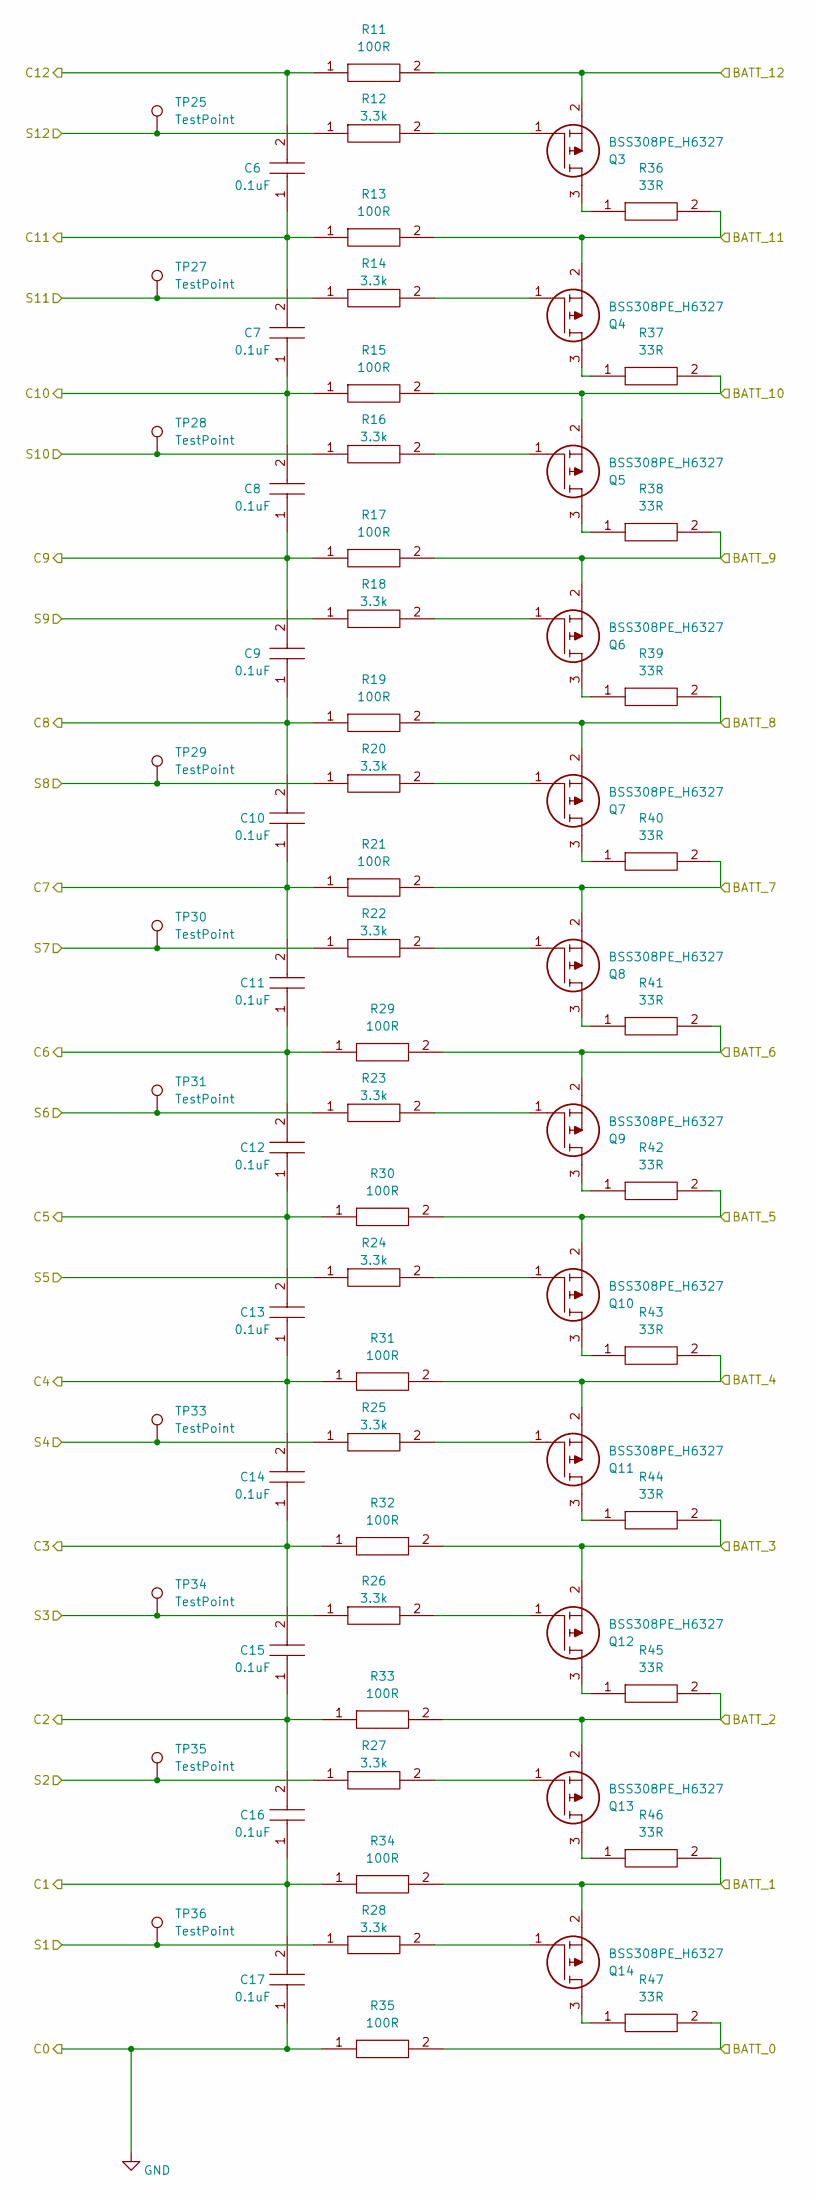
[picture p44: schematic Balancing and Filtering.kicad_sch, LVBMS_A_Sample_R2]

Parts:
C6, C7, C8, C9, C10, C11, C12, C13, C14, C15, C16, C17: 0.1uF; C_0603_1608Metric_Pad1.08x0.95mm_HandSolder; Manufacturer_Part_Number CC0805JRX7R9BB103
Q3, Q4, Q5, Q6, Q7, Q8, Q9, Q10, Q11, Q12, Q13, Q14: BSS308PE_H6327; SOT95P260X110-3N; Manufacturer_Part_Number BSS308PE H6327; Mouser Part Number 726-BSS308PEH6327
R11, R13, R15, R17, R19, R21, R29, R30, R31, R32, R33, R34, R35: 100R; R_0603_1608Metric_Pad0.98x0.95mm_HandSolder; Manufacturer_Part_Number ERJP06F1000V
R12, R14, R16, R18, R20, R22, R23, R24, R25, R26, R27, R28: 3.3k; R_0603_1608Metric_Pad0.98x0.95mm_HandSolder; Manufacturer_Part_Number ERJP06J332V
R36, R37, R38, R39, R40, R41, R42, R43, R44, R45, R46, R47: 33R; R_1206_3216Metric_Pad1.30x1.75mm_HandSolder; Manufacturer_Part_Number ERJ-P6WF33R0V; Mouser Part Number 667-ERJ-P6WF33R0V
TP25, TP27, TP28, TP29, TP30, TP31, TP33, TP34, TP35, TP36: TestPoint; TestPoint_Pad_D1.0mm

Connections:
/Balancing and Filtering/BATT_0: R35.2, R47.2; also elsewhere on the board
/Balancing and Filtering/BATT_1: Q14.2, R34.2, R46.2; also elsewhere on the board
/Balancing and Filtering/BATT_2: Q13.2, R33.2, R45.2; also elsewhere on the board
/Balancing and Filtering/BATT_3: Q12.2, R32.2, R44.2; also elsewhere on the board
/Balancing and Filtering/BATT_4: Q11.2, R31.2, R43.2; also elsewhere on the board
/Balancing and Filtering/BATT_5: Q10.2, R30.2, R42.2; also elsewhere on the board
/Balancing and Filtering/BATT_6: Q9.2, R29.2, R41.2; also elsewhere on the board
/Balancing and Filtering/BATT_7: Q8.2, R21.2, R40.2; also elsewhere on the board
/Balancing and Filtering/BATT_8: Q7.2, R19.2, R39.2; also elsewhere on the board
/Balancing and Filtering/BATT_9: Q6.2, R17.2, R38.2; also elsewhere on the board
/Balancing and Filtering/BATT_10: Q5.2, R15.2, R37.2; also elsewhere on the board
/Balancing and Filtering/BATT_11: Q4.2, R13.2, R36.2; also elsewhere on the board
/Balancing and Filtering/BATT_12: Q3.2, R11.2; also elsewhere on the board
/C1: C16.1, C17.2, R34.1; also elsewhere on the board
/C2: C15.1, C16.2, R33.1; also elsewhere on the board
/C3: C14.1, C15.2, R32.1; also elsewhere on the board
/C4: C13.1, C14.2, R31.1; also elsewhere on the board
/C5: C12.1, C13.2, R30.1; also elsewhere on the board
/C6: C11.1, C12.2, R29.1; also elsewhere on the board
/C7: C10.1, C11.2, R21.1; also elsewhere on the board
/C8: C9.1, C10.2, R19.1; also elsewhere on the board
/C9: C8.1, C9.2, R17.1; also elsewhere on the board
/C10: C7.1, C8.2, R15.1; also elsewhere on the board
/C11: C6.1, C7.2, R13.1; also elsewhere on the board
/C12: C6.2, R11.1; also elsewhere on the board
/S1: R28.1, TP36.1; also elsewhere on the board
/S2: R27.1, TP35.1; also elsewhere on the board
/S3: R26.1, TP34.1; also elsewhere on the board
/S4: R25.1, TP33.1; also elsewhere on the board
/S5: R24.1; also elsewhere on the board
/S6: R23.1, TP31.1; also elsewhere on the board
/S7: R22.1, TP30.1; also elsewhere on the board
/S8: R20.1, TP29.1; also elsewhere on the board
/S9: R18.1; also elsewhere on the board
/S10: R16.1, TP28.1; also elsewhere on the board
/S11: R14.1, TP27.1; also elsewhere on the board
/S12: R12.1, TP25.1; also elsewhere on the board
GND: C17.1, R35.1; also elsewhere on the board
unnamed: Q3.1, R12.2
unnamed: Q3.3, R36.1
unnamed: Q4.1, R14.2
unnamed: Q4.3, R37.1
unnamed: Q5.1, R16.2
unnamed: Q5.3, R38.1
unnamed: Q6.1, R18.2
unnamed: Q6.3, R39.1
unnamed: Q7.1, R20.2
unnamed: Q7.3, R40.1
unnamed: Q8.1, R22.2
unnamed: Q8.3, R41.1
unnamed: Q9.1, R23.2
unnamed: Q9.3, R42.1
unnamed: Q10.1, R24.2
unnamed: Q10.3, R43.1
unnamed: Q11.1, R25.2
unnamed: Q11.3, R44.1
unnamed: Q12.1, R26.2
unnamed: Q12.3, R45.1
unnamed: Q13.1, R27.2
unnamed: Q13.3, R46.1
unnamed: Q14.1, R28.2
unnamed: Q14.3, R47.1



Board: 2 copper layers, 48.2 x 53.5 mm, 132 parts (27 on the bottom side), 106 nets.

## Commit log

2019-12-22 Added template for 2020 temperature sensor
    [191212 Precharge Controller R0.PrjPcb, 191212 Temperature Sensors R0.PrjPcb, 191218 Current Detector PCB R1.PrjPcb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]
2019-12-29 Advancement in schematic for temperature sensor
    [039300020.stp, 039300040.stp, 039300060.stp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]
2019-12-30 Updated PCB layout for temperature sensors
    [191212 Temperature Sensors R0.PrjPcb, 4 Channel ADC.SchDoc, CAN.SchDoc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]
2020-01-05 Started work on brake module for ts_20 24V architecture
    [191228 Precharge Controller R1.PrjPcb, 200103 Brake Module R0.PrjPcb, 4 Channel ADC.SchDoc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]
2020-01-06 Advanced schematic for Brake Module, still needs safety loops to be added
    [191212 Temperature Sensors R0.PrjPcb, 200103 Brake Module R0.PrjPcb, BSPD.SchDoc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]
2020-01-08 Schematic at 50% for discharge module and additional changes to circuits to match them
    [200108 Discharge Module R0.PrjPcb, CAN.SchDoc, Current Sensor.SchDoc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]
2020-01-17 dicharge and temp board routing
    [Discharge.SchDoc, Microcontroller.SchDoc, Sensors.SchDoc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]
2020-02-02 New revision of ts_20 precharge controller
    [200130 Precharge Controller R2.PrjPcb, CAN.SchDoc, Digital Isolation.SchDoc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]
2020-02-07 Smaller sense resistors for HV
    [200130 Precharge Controller R2.PrjPcb, CAN.SchDoc, HV Sense.SchDoc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]
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2020-02-12 Added power calculations for discharge and precharge
    [200130 Precharge Controller R2.PrjPcb, Discharge.SchDoc, Flasher.SchDoc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]
2020-02-15 additional changes to the brake module
    [200108 Discharge Module R0.PrjPcb, 200130 Precharge Controller R2.PrjPcb, Power Supply.SchDoc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]
2020-02-15 Hardcore routing of ts_20 precharge newwwwwwwww
    [200130 Precharge Controller R2.PrjPcb, Safety Loops.SchDoc, Top Level.SchDoc]
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2020-02-19 Completed precharge PCB routing awaiting approval
    [Digital Isolation.SchDoc, Microcontroller.SchDoc, Power Supply.SchDoc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]
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2020-02-20 updated part number for capacitor
    [ts_20-standard-library-database.xls]
2020-02-21 Updated version of UCM, 2020 edition, a modern classic
    [200221 UCM R0.PrjPcb, 4 Channel ADC.SchDoc, CAN.SchDoc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]
2020-02-21 Added review copy and line notes for precharge controller
    [200130 Precharge Controller R2.PrjPcb, Microcontroller.SchDoc, PCB.PcbDoc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]
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2020-02-27 Updated library with 556 timer
    [ts_20-standard-library-database.xls]
2020-02-27 New components and modifications to discharge and precharge
    [200222 Discharge Module R1.PrjPcb, 200226 BMS Master R0.PrjPcb, 200226 Precharge Controller R3.PrjPcb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]
2020-02-27 New Brake Module Revision
    [200103 Brake Module R1.PrjPcb, 4 Channel ADC.SchDoc, BSPD.SchDoc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]
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2020-02-27 added 556 in library database
    [ts_20-standard-library-database.xls]
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2020-02-28 added ltc6820 and began routing discharge
    [200222 Discharge Module R1.PrjPcb, 200226 BMS Master R0.PrjPcb, 200228 BMS Slave R0.PrjPcb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]
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2020-03-02 Added R6015ENJTL to library
    [AAI.PcbDoc, AAI.SchDoc, ts_20-standard-library-database.xls]
2020-03-02 Routed Accumulator Active Light
    [AAI.PcbDoc, AAI.SchDoc, ts-20-Accumulator-Active-Indicator.PrjPcb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]
2020-03-02 Add files via upload
    Manually Uploading Brake Module ~enjoy
    [200103 Brake Module R1.PrjPcb, 4 Channel ADC.SchDoc, BSPD.SchDoc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]
2020-03-02 Add files via upload
    Formatted Updates
    [200103 Brake Module R1.PrjPcb, 4 Channel ADC.SchDoc, BSPD.SchDoc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]
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2020-03-06 Added the damn header for the 10th time
    [200306 Discharge Module R2.PrjPcb, 5kW Sensor.SchDoc, CAN.SchDoc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]
2020-03-06 Hey ben, i've figured out why the header isn't getting added. In Windows, if a file is active, it is not able to be written to, so when Altium is open, it's using the excel file, and as such, cannot 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
    [200306 Discharge Module R2.PrjPcb, 5kW Sensor.SchDoc, CAN.SchDoc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]
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2020-03-17 Added new HV logo and additional finalisations for precharge controller
    [logos.PcbLib]
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2020-03-18 minor correction
    [DT.PcbLib, DT.SchLib, Top Level.SchDoc]
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2020-03-19 New components, and finalisation of PI CAN interface
    [200318 Universal Pi CAN Interface.PrjPcb, CAN.SchDoc, Microcomputer.SchDoc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]
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2020-03-27 Approaching ready for manufacturing for precharge and discharge PCBs
    [200306 Discharge Module R2.PrjPcb]
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2020-03-31 Fixed molex library
    [039293026.stp, 039293046.stp, 039293086.stp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]
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2020-04-04 More changes to the header library and precharge controller additional stuff for notes
    [200226 Precharge Controller R3.PrjPcb, Top Level.SchDoc, integrated.SchLib]
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2020-04-16 Ben i love you, but for the love of god, stop breaking Git
    [Output Driver.SchDoc]
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2020-04-30 UCM Fix
    [200221 UCM R1.PrjPcb, CAN.SchDoc, Generic.PcbLib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]
2020-04-30 Terminal Board UCM, fixes
    [200221 UCM R1.PrjPcb, 200415 Brake Module R5.PrjPcb, 310320 Terminal Board R2.PrjPcb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]
2020-05-03 UCM Antonio Fixes
    [200306 Discharge Module R2.PrjPcb]
2020-05-04 UCM pour fixes
    [DT.PcbLib, Generic.PcbLib]
2020-05-04 UCM fixes 5-05-20
    [Output Driver.SchDoc, Top Level.SchDoc]
2020-05-05 Footprint Fixs
    [Top Level.SchDoc]
2020-05-05 Fixed UCM
    [200226 Precharge Controller R3.PrjPcb]
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2020-05-08 analog mistake
    [Microcontroller.SchDoc, TSAL.PcbDoc, logos.PcbLib]
2020-05-09 Library Update and footprint fixes
    [200421 BSPD Current Detector R1.PrjPcb, DT.PcbLib, Top Level.SchDoc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]
2020-05-09 Added missing footprint
    [logos.PcbLib]
2020-05-10 Disco Fix
    [PCB1.PcbDoc]
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2020-06-02 Here's a gift Ben and Tom, plug the IMU into anywhere, Love Patrick
    [1 3 OLED ICC .STEP, Interface.SchDoc, Make My IMU Work Anywhere.PrjPcb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]
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2020-08-08 Changes to reflow oven/dischrage. Minor revisions for assisting readability
    [LED MODULE.SchDoc, Microcontroller.SchDoc, PCB.PcbDoc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]
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2020-08-19 Trolly Discharge R2 with better clearance
    [PCB.PcbDoc, Power.SchDoc, Switch.SchDoc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]
2020-08-22 More little notes for the little mistakes we make along the way :)
    [CAN.SchDoc]
2020-08-23 Added stm32f446 to library & adjusted 3.3V regulator symbol
    [Microcontroller (F446).SchDoc, STM32F446RET6--3DModel-STEP-56544.STEP, STM32F466 TEST.PrjPcb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]
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2020-08-25 Missed can2 tx
    [Microcontroller (F446).SchDoc, integrated.SchLib]
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2020-08-27 Switching to GLV for relay on Trolly Discharge
    [PCB.PcbDoc, Power.SchDoc, Switch.SchDoc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]
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2020-12-30 Fix Footpath not found on some connectors
    [ts_20-standard-connectors-database.xls]
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2021-03-25 Fix for UCM (Jumper wires. Still Needs PWM Pins and replaced Digital IC)
    [Microcontroller.SchDoc]
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2021-05-04 Fix PWM Pins on UCM
    [200221 UCM R1.PrjPcb, Microcontroller.SchDoc, Power Supply.SchDoc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]
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2021-06-26 added some precharge stuff and changed database references
    [CAN.SchDoc, Power Supply.SchDoc, Top Level.SchDoc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]
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2021-06-28 Changes made to break module to fix jumper leads. (Needs to be checked by Nam or Ben).
    [200415 Brake Module R6.PrjPcb, BSPD.SchDoc, CAN.SchDoc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]
2021-07-07 Brake Module Fixes (Needs to be check by Ben)
    [BSPD.SchDoc, Isolation.SchDoc, Microcontroller.SchDoc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]
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2021-09-25 Routed Precharge GLV section and added JST xh
    [CAN.SchDoc, HV Sense.SchDoc, JST - XH - Thru V - 10Pin - 2.54mm.stp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]
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
